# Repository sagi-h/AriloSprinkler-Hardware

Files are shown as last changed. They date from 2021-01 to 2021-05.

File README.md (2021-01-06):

# AriloSprinkler-Hardware
OpenSprinkler ESP32-WROOM Hardware Design variant including a Lora E22-900M30S-SX1262 and made in Kicad software.

HW features:
- 8 valve AC driver compatible with OpenSprinkler Zone Expanders
- Lora E22-900M30S-SX1262 long range transceiver (up to 30dBm)
- USB interface for debugging/flashing
- Ethernet interface (Exemplary module: https://de.aliexpress.com/item/2042562851.html?spm=a2g0s.9042311.0.0.27424c4daFHBJU)
- RF Transmitter interface (Exemplary module: https://de.aliexpress.com/item/4001119703303.html?spm=a2g0s.9042311.0.0.27424c4daFHBJU)
- Compatible with DIN rails (Used holding system: https://de.aliexpress.com/item/32827395562.html?spm=a2g0s.9042311.0.0.27424c4daFHBJU)
- Reworked current measurement with inverted precision rectifier required due to the ADC of the ESP32
- RTC
- Button switches

Tested features:
- Opensprinkler SW features work
- Lora transceiver works
- Current measurement works
- Valve control works
- Button switches work

All parts have a LCSC reference number and are at the time of writting this readme available in the JLCPCB SMT library. I have got my prototype boards produced by JLCPCB (quite inexpensive, 5 full SMT assembled and shipped PCB's for arround 75€, additionally E22 module, ESP32 and USB and SMT connectors to be added).

The compatible SW can be found in the following OpenSprinkler Firmware branch:
https://github.com/arijav/AriloSprinkler-Firmware

Note: This is a home made prototype. No guarantee of any kind is given. If you want a commercial product please order the regular OpenSprinkler official parts.

Final design (not yet produced, use at your own risk):

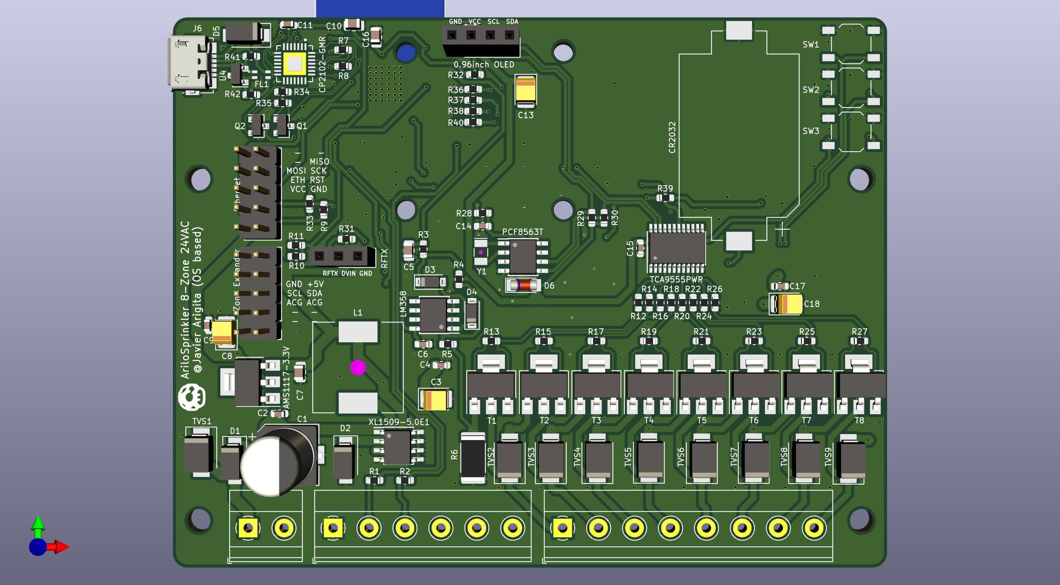
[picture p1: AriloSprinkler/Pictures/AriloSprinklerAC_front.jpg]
Final design front

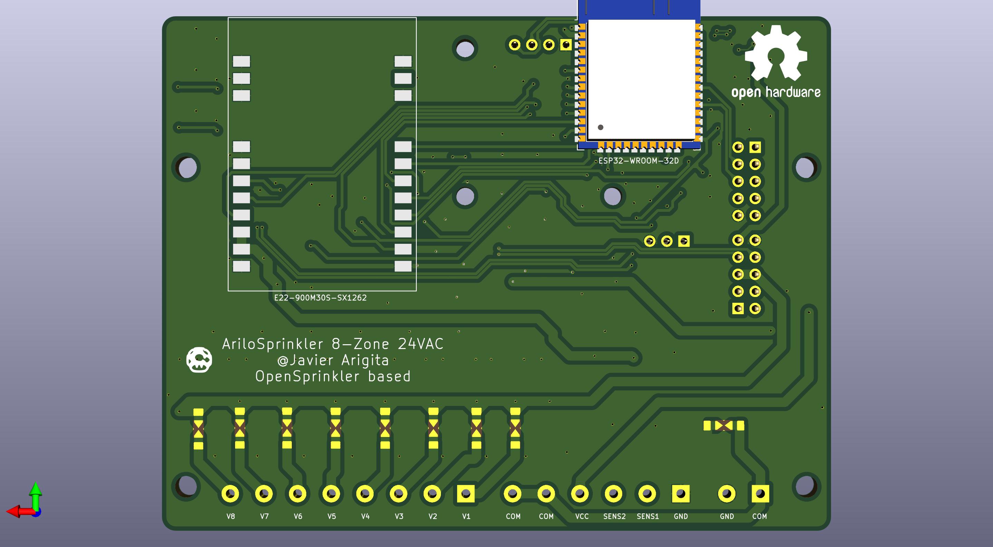
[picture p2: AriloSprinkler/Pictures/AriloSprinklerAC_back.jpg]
Final design back


Prototype:

Prototype front
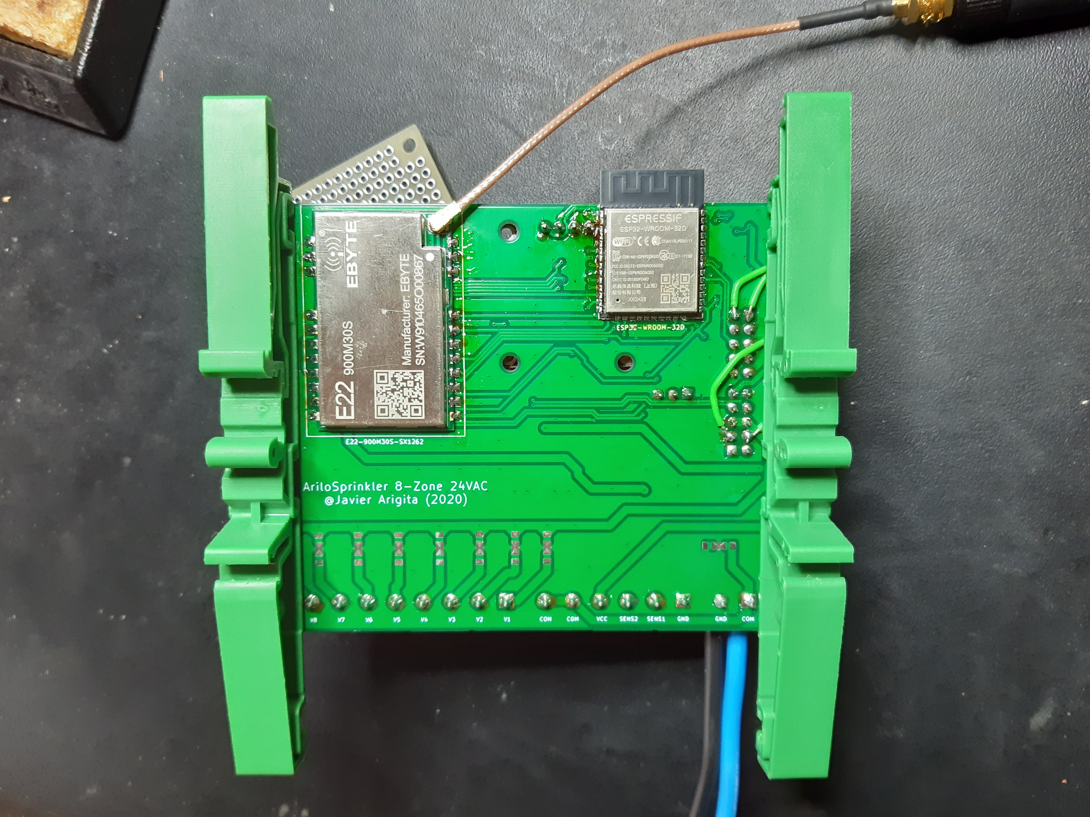
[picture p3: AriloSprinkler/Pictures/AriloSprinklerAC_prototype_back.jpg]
Prototype back


For questions send a message to:
gmail email: arijav2020

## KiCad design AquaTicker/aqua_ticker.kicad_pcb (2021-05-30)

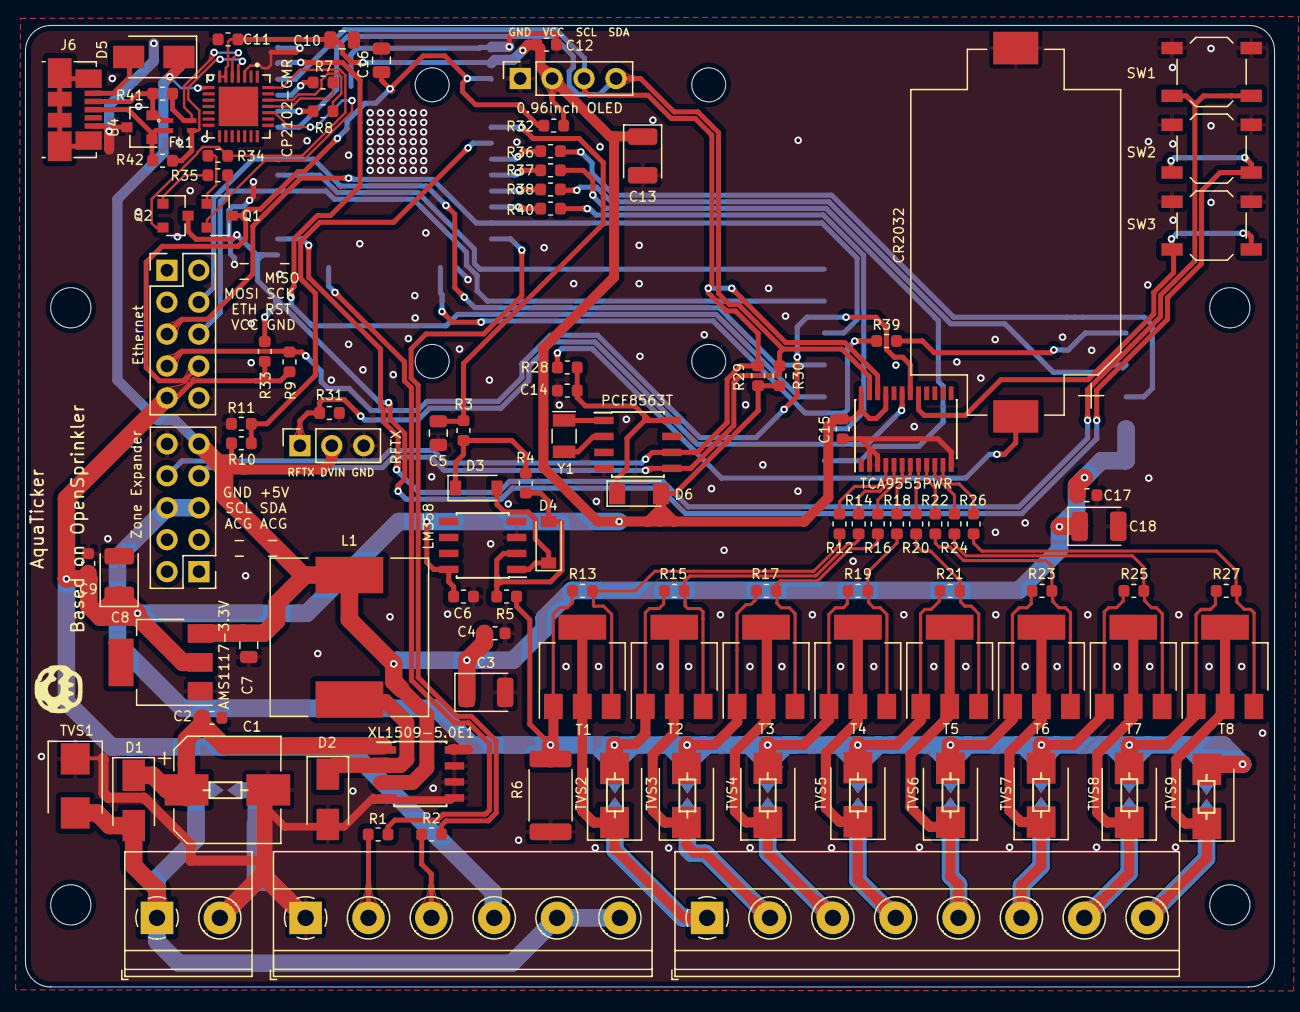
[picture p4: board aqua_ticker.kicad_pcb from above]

Board: 2 copper layers, 99.4 x 76.5 mm, 118 parts (0 on the bottom side), 80 nets.

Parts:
BT1: CR2032; BatteryHolder_Keystone_1060_1x2032
C1: 100uF; CP_Elec_8x10
C2, C4, C6, C9, C11, C12, C14, C15, C17: 0.1u; C_0603_1608Metric
C3, C8, C13, C18: 100uF; CP_EIA-3528-21_Kemet-B
C5, C7, C10: 10u; C_0805_2012Metric
C16: 1u; C_0805_2012Metric
D1, D5: M7; D_SMA
D2: SS34; D_SMA
D3, D4: DN4148; D_SOD-123
D6: LL4148; D_MiniMELF
FL1: ACM2012-121-2P-T002; FIL_ACM2012-121-2P-T002
J1: M024MM-X; TerminalBlock_Phoenix_MKDS-1,5-2_1x02_P5.00mm_Horizontal
J2: M065MM; TerminalBlock_Phoenix_MKDS-1,5-6_1x06_P5.00mm_Horizontal
J3: RFTX; PinSocket_1x03_P2.54mm_Vertical
J4: Ethernet; PinHeader_2x05_P2.54mm_Vertical
J5: Zone Expander; PinHeader_2x05_P2.54mm_Vertical
J6: USB_B_Micro; USB_Micro-B_Molex_47346-0001
J7: M085MM-8; TerminalBlock_Phoenix_MKDS-1,5-8_1x08_P5.00mm_Horizontal
J8: 0.96inch OLED; PinSocket_1x04_P2.54mm_Vertical
L1: 68uH; L_12x12mm_H6mm
Q1, Q2: Q_NPN_BCE; SOT-23
R1, R2, R34, R35: 4K7; R_0603_1608Metric
R3: 100; R_0603_1608Metric
R4: 300K; R_0603_1608Metric
R5, R10, R11: 100K; R_0603_1608Metric
R6: 0.20; R_2512_6332Metric
R7, R8: 470; R_0603_1608Metric
R9, R28, R32: 10K; R_0603_1608Metric
R12, R14, R16, R18, R20, R22, R24, R26: 390; R_0603_1608Metric
R13, R15, R17, R19, R21, R23, R25, R27: 470K; R_0603_1608Metric
R29, R30, R31, R33: 1K; R_0603_1608Metric
R36, R37, R38, R39, R40: 22R; R_0603_1608Metric
R41, R42: 10; R_0603_1608Metric
SP1, SP2, SP3, SP4, SP5, SP6, SP7, SP8, SP9: PCB-SGAP
SW1, SW2, SW3: SW_SPST; SW_SPST_TL3342
T1, T2, T3, T4, T5, T6, T7, T8: Z0103MN5AA4; SOT-223
TVS1: 43CA; D_SMB
TVS2, TVS3, TVS4, TVS5, TVS6, TVS7, TVS8: SMBJ43CA; D_SMB
TVS9: TVSSMB; D_SMB
U1: XL1509-5.0E1; SOIC-8_3.9x4.9mm_P1.27mm
U2: LM358; SOIC-8_3.9x4.9mm_P1.27mm
U3: AMS1117-3.3V; SOT-223
U4: PSM712-LF-T7; SOT-23
U5: CP2102-GMR; QFN50P500X500X100-29N
U6: ESP32-WROOM-32D; ESP32-WROOM-32
U7: PCF8563T; SOIC-8_3.9x4.9mm_P1.27mm
U8: TCA9555PWR; TSSOP-24_4.4x7.8mm_P0.65mm
U9: E22-900M30S-SX1262
Y1: Crystal_Small; Crystal_SMD_G8-2Pin_3.2x1.5mm

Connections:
/ACRET: J5.5, J5.6, R5.1, R6.1, R13.2, R15.2, R17.2, R19.2, R21.2, R23.2, R25.2, R27.2, SP2.2, SP3.2, SP4.2, SP5.2, SP6.2, SP7.2, SP8.2, SP9.2, T1.1, T2.1, T3.1, T4.1, T5.1, T6.1, T7.1, T8.1, TVS2.2, TVS3.2, TVS4.2, TVS5.2, TVS6.2, TVS7.2, TVS8.2, TVS9.2
/BUSY: R40.2, U9.14
/COM: D1.2, J1.1, J2.5, J2.6, SP1.2, TVS1.2
/D+: FL1.2, J6.3, R42.1, U4.1
/D-: FL1.1, J6.2, R41.2, U4.2
/DADC: C5.1, R3.1, U6.6
/DIO1: R37.2, U9.13
/DIO2: R36.2, U9.8
/DM: FL1.4, R41.1, U5.5
/DP: FL1.3, R42.2, U5.4
/DSCL: J5.8, J8.3, R29.2, U6.36, U7.6, U8.22
/DSDA: J5.7, J8.4, R30.2, U6.33, U7.5, U8.23
/DTR: Q2.2, R34.2, U5.28
/DVIN: C3.1, C4.1, C7.1, C17.1, C18.1, D5.1, J3.2, J5.9, L1.2, R11.1, U1.3, U3.3, U5.8, U9.9, U9.10
/DVINSENS: R10.1, R11.2, U6.7
/ETH: J4.7, R9.2, U8.18
/GPIO0: Q2.3, R33.2, SW2.1, U6.25
/IO13: R39.1, U6.16
/IO25: R38.1, U6.10
/IO26: R40.1, U6.11
/IO32: R36.1, U6.8
/IO33: R37.1, U6.9
/MISO: J4.4, U6.31, U9.16
/MOSI: J4.5, U6.12, U9.17
/NSS_SEL: U6.30, U9.19
/P0: R12.1, U8.4
/P1: R14.1, U8.5
/P2: R16.1, U8.6
/P3: R18.1, U8.7
/P4: R20.1, U8.8
/P5: R22.1, U8.9
/P6: R24.1, U8.10
/P7: R26.1, U8.11
/RESET: U6.37, U9.15
/RFTX: J3.1, R31.1, U8.19
/RST: C16.1, J4.8, Q1.3, R32.1, U6.3
/RTS: Q1.2, R35.2, U5.24
/RXD: R8.2, U6.34
/RXEN: R39.2, U9.6
/SCK: J4.6, U6.29, U9.18
/SENS1: R1.2, U6.23
/SENS2: R2.2, U6.13
/SW1: SW1.1, U6.26
/SW3: SW3.1, U8.17
/TXD: R7.2, U6.35
/TXEN: R38.2, U9.7
/VBUS: D5.2, J6.1
/VCC: C6.1, C8.1, C9.1, C10.1, C11.1, C12.1, C13.1, C15.1, D6.2, J2.4, J4.9, J8.2, R9.1, R29.1, R30.1, R32.2, R33.1, U2.8, U3.2, U5.6, U5.7, U6.2, U8.21, U8.24
GND: BT1.2, C1.2, C2.2, C3.2, C4.2, C5.2, C6.2, C7.2, C8.2, C9.2, C10.2, C11.2, C12.2, C13.2, C14.2, C15.2, C16.2, C17.2, C18.2, D2.2, J1.2, J2.1, J3.3, J4.10, J5.10, J6.5, J8.1, R6.2, R10.2, R31.2, SP1.1, SW1.2, SW2.2, SW3.2, TVS1.1, U1.4, U1.5, U1.6, U1.7, U1.8, U2.3, U2.4, U3.1, U4.3, U5.3, U6.1, U6.15, U6.38, U6.39, U7.4, U8.2, U8.3, U8.12, U9.1, U9.2, U9.3, U9.4, U9.5, U9.11, U9.12, U9.20, U9.22
unnamed: BT1.1, R28.2
unnamed: C1.1, C2.1, D1.1, U1.1
unnamed: C14.1, D6.1, R28.1, U7.8
unnamed: D2.1, L1.1, U1.2
unnamed: D3.1, R3.2, R4.2
unnamed: D3.2, D4.1, U2.1
unnamed: D4.2, R4.1, R5.2, U2.2
unnamed: J2.2, R1.1
unnamed: J2.3, R2.1
unnamed: J7.1, SP2.1, T1.2, T1.4, TVS2.1
unnamed: J7.2, SP3.1, T2.2, T2.4, TVS3.1
unnamed: J7.3, SP4.1, T3.2, T3.4, TVS4.1
unnamed: J7.4, SP5.1, T4.2, T4.4, TVS5.1
unnamed: J7.5, SP6.1, T5.2, T5.4, TVS6.1
unnamed: J7.6, SP7.1, T6.2, T6.4, TVS7.1
unnamed: J7.7, SP8.1, T7.2, T7.4, TVS8.1
unnamed: J7.8, SP9.1, T8.2, T8.4, TVS9.1
unnamed: Q1.1, R34.1
unnamed: Q2.1, R35.1
unnamed: R7.1, U5.25
unnamed: R8.1, U5.26
unnamed: R12.2, R13.1, T1.3
unnamed: R14.2, R15.1, T2.3
unnamed: R16.2, R17.1, T3.3
unnamed: R18.2, R19.1, T4.3
unnamed: R20.2, R21.1, T5.3
unnamed: R22.2, R23.1, T6.3
unnamed: R24.2, R25.1, T7.3
unnamed: R26.2, R27.1, T8.3
unnamed: U7.1, Y1.1
unnamed: U7.2, Y1.2

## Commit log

2021-01-06 Initial AriloSprinkler HW commit
    [acdr_3.0.brd, acdr_3.0.sch, acdr_3.1.brd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]
2021-04-14 kicad_plugins: remove teardrop plugin
2021-04-14 kicad: add lib table files
2021-04-14 gitignore: update with kicad files
2021-05-30 AquaTicker initial commit
    [aqua_ticker.kicad_pcb, aqua_ticker.sch, arilo_sprinkler.sch]
